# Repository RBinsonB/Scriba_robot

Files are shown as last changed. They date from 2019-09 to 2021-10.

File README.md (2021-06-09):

# Scriba robot
More information (such as components used, robot building and so on) can be found on the [Hackster page of the project.](https://www.hackster.io/robinb/scriba-robot-a-printing-robot-0048fa).

ROS code has been moved to dedicated repositories.
- [scriba_ros](https://github.com/RBinsonB/scriba_ros): robot base packages (for bringup, motor command, odometry)
- [scriba_localization](https://github.com/RBinsonB/scriba_localization): robot localization related packages (EKF, camera localization)

## Concept
Scriba is a printing robot. It prints on its wake, using the sheet edges and the printing in process as a reference for its navigation. It uses multiple cameras to correct its trajectory and printing alignment through a SLAM algorithm

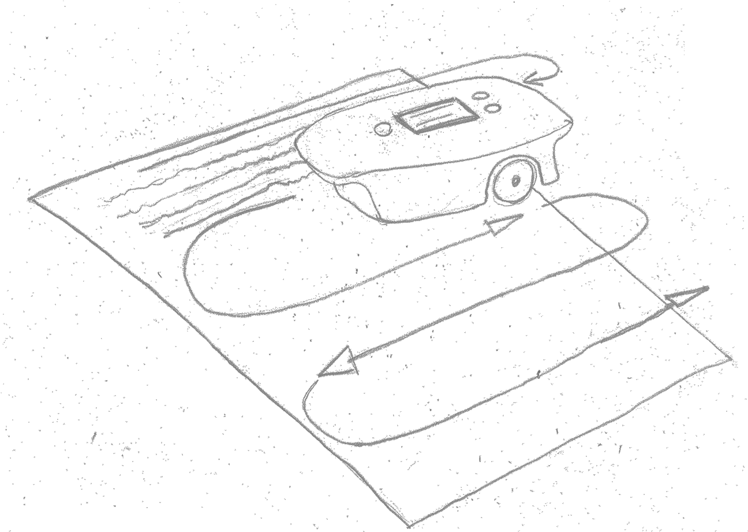
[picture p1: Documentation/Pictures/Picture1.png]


*Robot concept*

The robot was supposed to be light and portable but grew in sized as the project progressed. It is designed to print on medium and large surfaces.

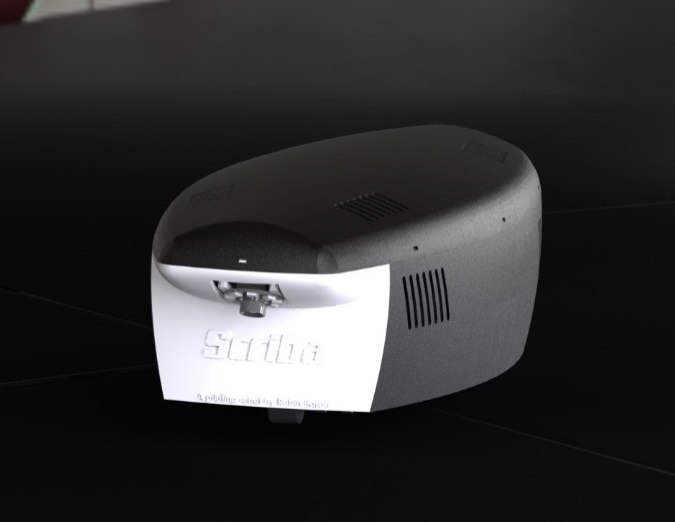
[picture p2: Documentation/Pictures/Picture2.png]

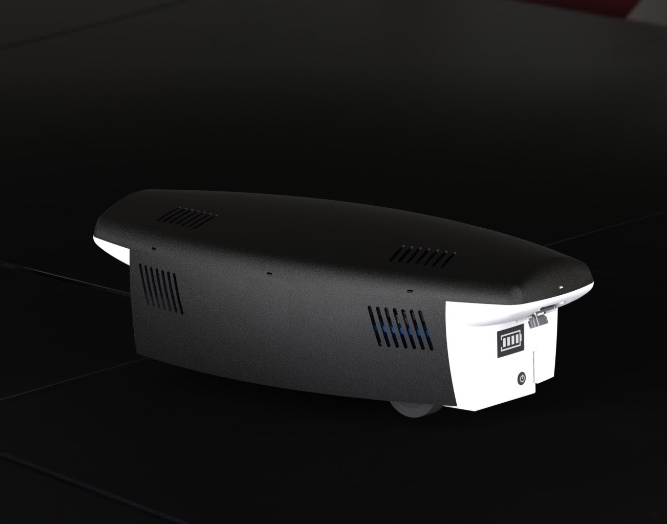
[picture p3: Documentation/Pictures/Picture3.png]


## Project advancement
WORK IN PROGRESS

Done:
```diff
+ Mechanical Design
+ Electrical Design
+ Components printing/machining
+ Robot assembly
+ PCB assembly
+ ROS serial communication with Arduinos
+ Standard motor command
+ Odometry
+ Odometry and motor command calibration
```
To do:
```diff
- Printhead test
- Low voltage disconnect board
- Step motor command
- Printing command
- Localization by camera
```
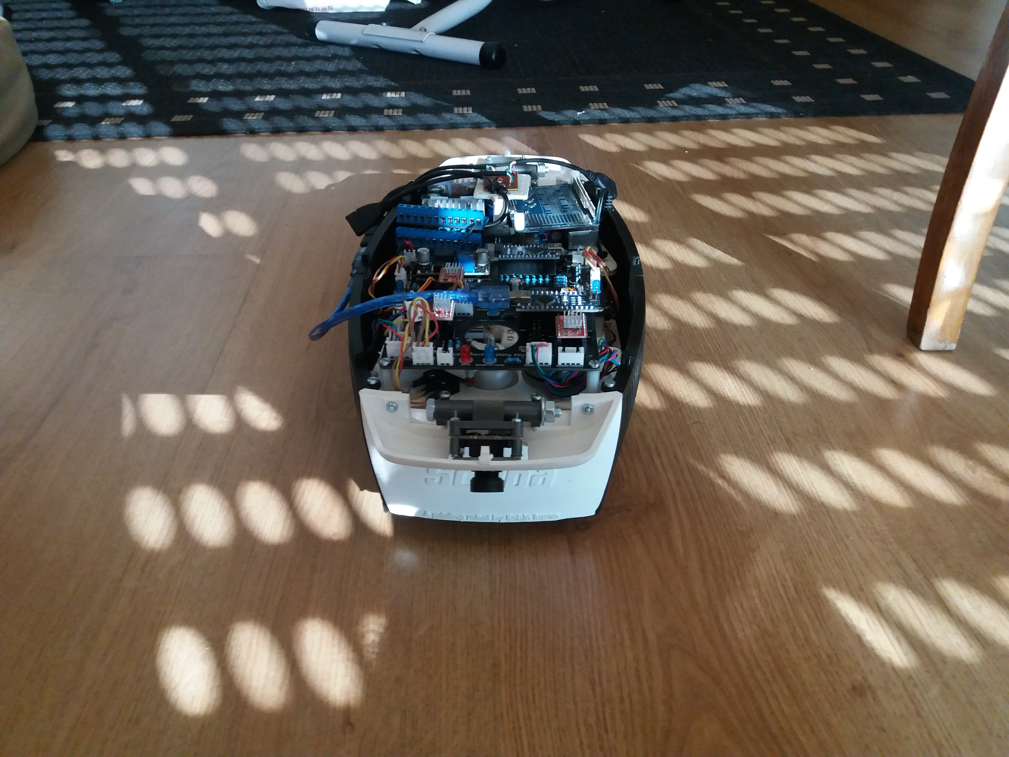
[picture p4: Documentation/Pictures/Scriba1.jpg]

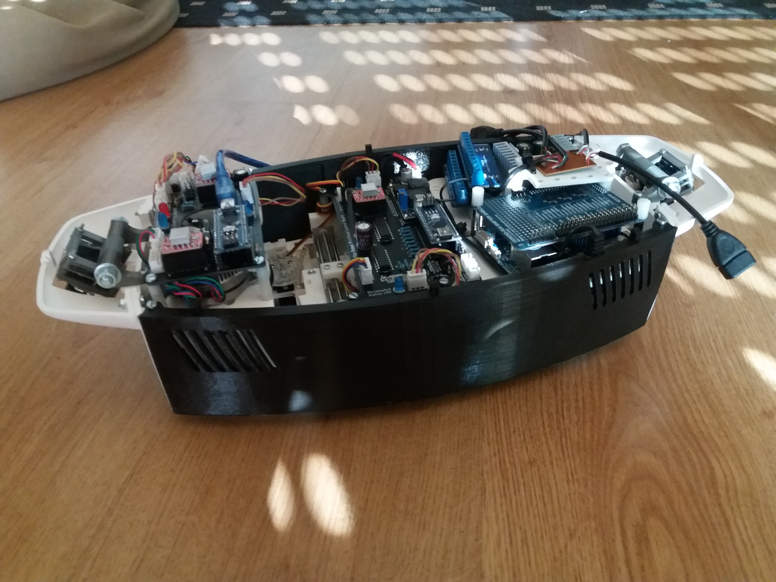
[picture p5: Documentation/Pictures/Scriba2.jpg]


### Video: Scriba drive & odometry test
Scriba odometry test (https://www.youtube.com/watch?v=UUCUU0tR3d4)
### Video: Scriba front wheel calibration 
Scriba front wheel angle calibration (https://www.youtube.com/watch?v=NhuQ65PKyDQ)

## System overview
The detailed [technical design description can be found here.](https://raw.githubusercontent.com/RBinsonB/Scriba_robot/master/Technical_Design_Scriba.pdf)

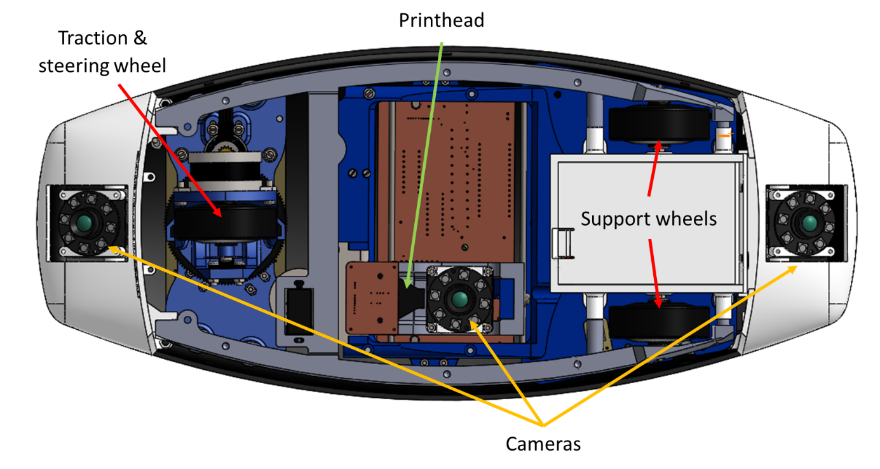
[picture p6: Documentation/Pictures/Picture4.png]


*Scriba robot bottom view*

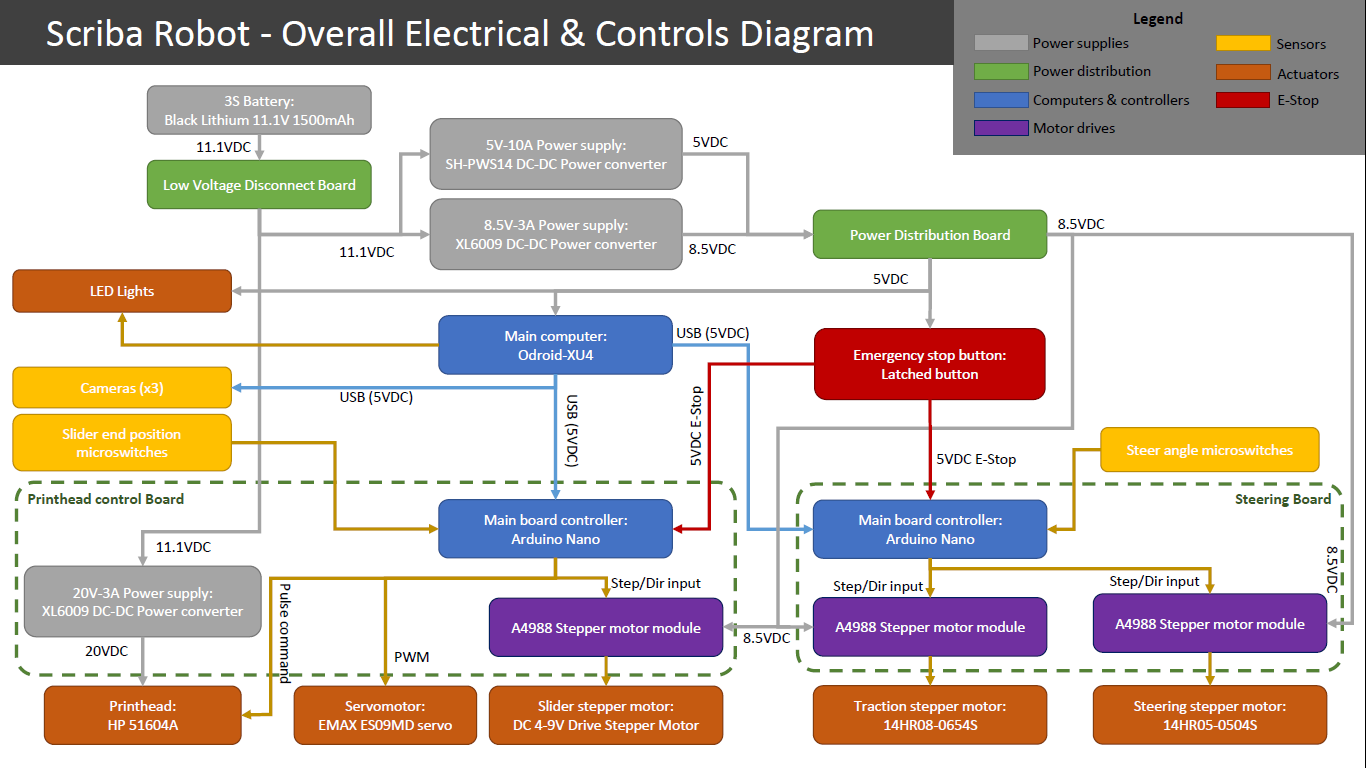
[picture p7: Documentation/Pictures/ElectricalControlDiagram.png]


*Overall electric & controls diagram*

[The diagram can be found here in higher resolution](https://raw.githubusercontent.com/RBinsonB/Scriba_robot/master/Overall_Electrical_&_Controls_Diagram_Scriba_Robot.pdf)

### Controls
The main computer of the robot is an Odroid-XU4 running Ubuntu 18.04 and mainly relying on a ROS (Robot Operating System) program to run the robot. Computer vision tasks are carried out by OpenCV programs interfaced with the ROS main program.

Actuator control is carried out by two Arduinos Nano, as they can handle real-time operation and GPIO control better than the main computer. They are connected to serial node on the ROS main program.
The robot can be controlled by WiFi from a remote computer by connecting to the Odroid-XU4 via SSH.

### Drive configuration
The robot has a steer drive configuration (also called steerable driving wheel configuration) with one powered and steering wheel at the front and 2 wheel for support at the rear (like a tricycle). This configuration was chosen because of the high driving accuracy it provides when following a navigation path.

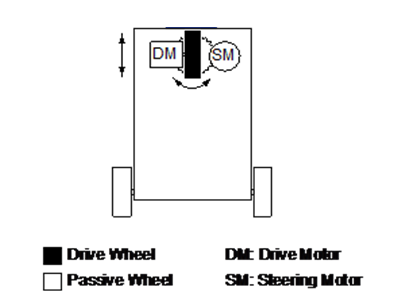
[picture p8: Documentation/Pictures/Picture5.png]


*Steer Drive configuration*

### Navigation & Localization system
The robot uses a SLAM algorithm (Simultaneous Localization And Mapping) to navigate. It localize itself by using the printing in process as a reference.

Cameras are located at the front and at the rear of the robot. Their location allows the robot to see the printing in process (with the rear camera) and the previous printing. Being able to see the previous printing after a turn is crucial to correct localization because turns generate a lot of imprecisions in the odometry.

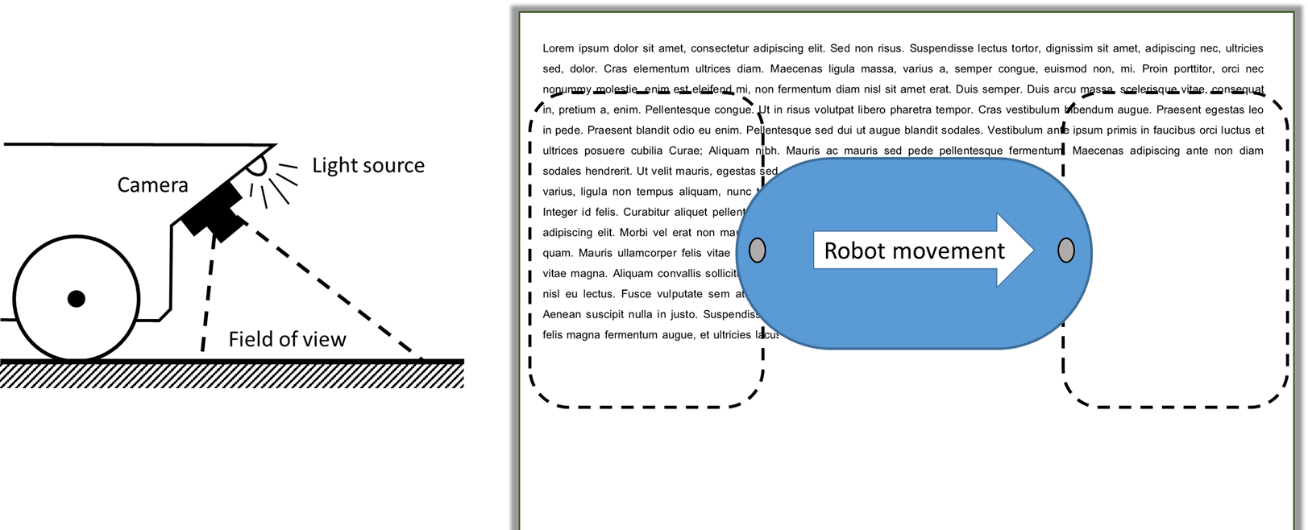
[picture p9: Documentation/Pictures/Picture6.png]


A light source near the camera ensures a correct and uniform lighting of the scanned surface. Inclination of the camera images is corrected by a homographic algorithm.

### Printing system
The printhead is placed on a sweeping system. Both have to stay perpendicular to the printing direction even when the robot is correcting its trajectory. The printing system is therefor able to rotate around the kinematic center of the robot.

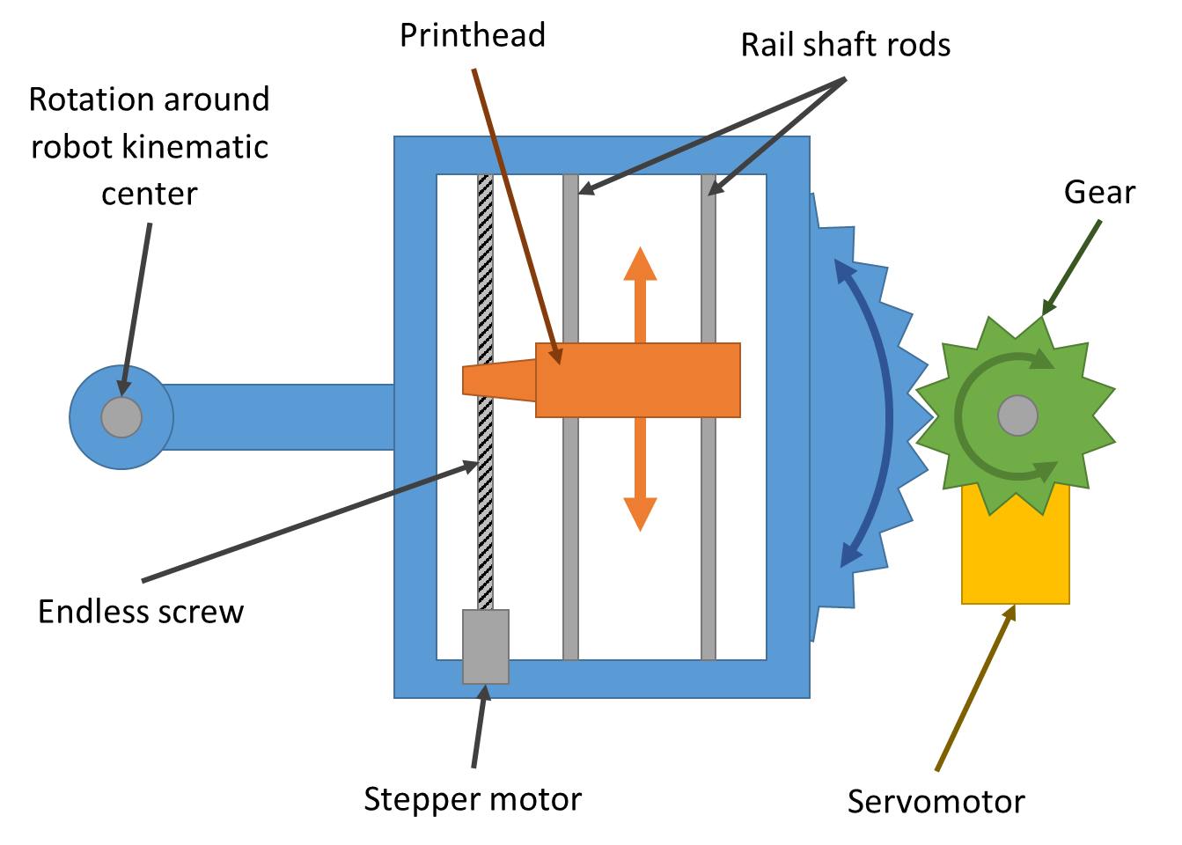
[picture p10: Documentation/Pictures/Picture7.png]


*Printing system schematics*

## Code description:
* Arduino: includes Arduino programs.
  * Programs:
    * *Scriba_steering_board_V1*: Program for the arduino of the drive unit. Uses custom message type to receive and execute motor commands, send odometry data and perform calibration operations.
    * *Scriba_steering_board_V2*: Updated version of the firmware to work with potentiometer on the front wheel steer angle.

## Authors

* **Robin Baran** - *Initial work*

## License

This project is licensed under the GNU General Public License version 3

## Acknowledgments

* [Inkjet Printer For the Reprap](https://reprap.org/mediawiki/images/1/1a/Inkjet.pdf) by Amberish Jaipuria
* [DIY Inkjet Printer](https://www.thingiverse.com/thing:8542/) by Patrick Hannan, Jared Knutzen, Nicholas C Lewis, Joy Markham

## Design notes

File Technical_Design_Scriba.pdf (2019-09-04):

Robin Baran | Scriba Robot - Technical Design | 1

## Scriba Robot – Technical Design

This document aims to describe the technical design of the Scriba robot. It includes mechanical design, electronics and code.

## Summary

## 1 Design Overview

### 1.1 Drive unit

1.1.1 Overall design
The traction and steering motor are assembled in a “drive unit” placed at the front of the robot.

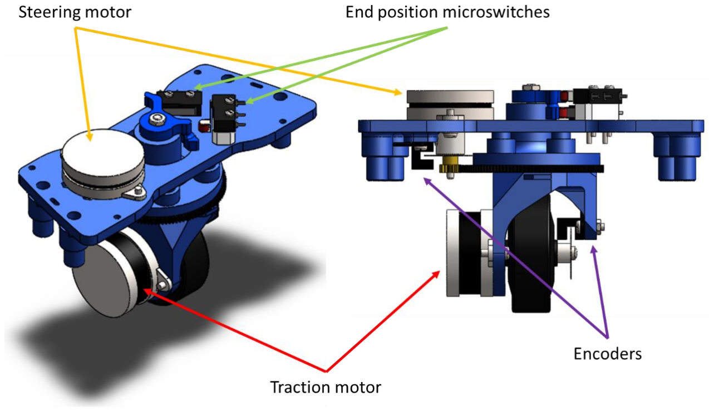
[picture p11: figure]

Figure 1: Drive unit

The driving wheel is powered by a stepper motor (14HR08-0654S) with a step angle resolution of 0.9 deg. In addition an encoder counts the rotation angle with a resolution of 1.8deg.

The driving wheel is steered by a stepper motor (14HR05-0504S) with a step angle resolution of 0.9 deg. In addition an encoder counts the rotation angle with a resolution of 1.8deg. The system is designed to rotate the driving wheel +/-90°.

Taking in account gears and microstepping configuration (rms), the relation between steering motor step and wheel angle (φ) is:

φ = steps ∗ angle by step ∗ rms ∗ (
zmot

zgear)

φ = steps ∗ rms ∗ 0.9 ∗ (

16
120) = steps ∗ rms ∗ 0.12

To recap the possible results:

Microstepping
configuration

Wheel angle (φ) for 1 step in degrees
Full step | 0.12°
1/2 step | 0.06°
1/4 step | 0.03°
1/8 step | 0.015°
1/16 step | 0.0075°

Two microswitches are used to detect the end position for calibration purposes: the starting angle of the wheel is unknown and a calibration is required before driving the robot. The microswitches are placed on slotted holes and can be adjusted.

1.1.2 Electronics
The stepper motors are controlled by an Arduino Nano and two A4988 modules. All those elements and connections for encoders, microswitches, and so on are integrated into a PCB (named “Steering Board”).

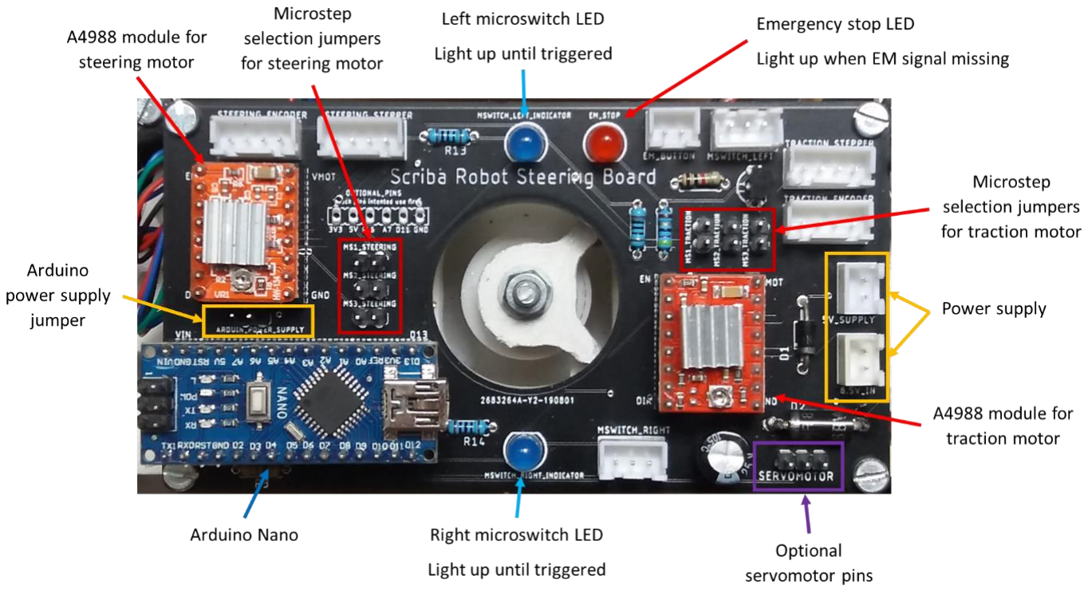
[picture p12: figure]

Figure 2: Steering Board

The board needs 5V and 8.5V power supplies. The 5V can be supplied by the Arduino if the Arduino power supply jumper is connected.

1.1.2.1 Microstepping selection
Stepper microstepping can be configured by the use of jumpers on the board. Connecting a jumper sets the microstep pin to high.

The truth table for the MS pins logic is the following:

MS1 MS2 MS3 | Microstep Resolution
Low | Low | Low | Full step
High | Low | Low | Half step
Low | High | Low | Quarter step
High | High | Low | Eighth step
High | High | High | Sixteenth step

1.1.2.2 Emergency stop
An emergency stop feature prevents the motors from running without a 5V input on the emergency stop connector. The emergency stop red LED lights when the signal is absent.

1.1.3 Program & Control
The unit is driven by an Arduino Nano. The Arduino is connected to the main computer of the robot, the Odroid-XU4 by USB.

The program on the Arduino connects to a serial node of the ROS main program.

### 1.2 Printing system

1.2.1 Overall design
The printing system is assembled on a rotating support (rotating around the robot kinematic center) to correct the alignment if needed.

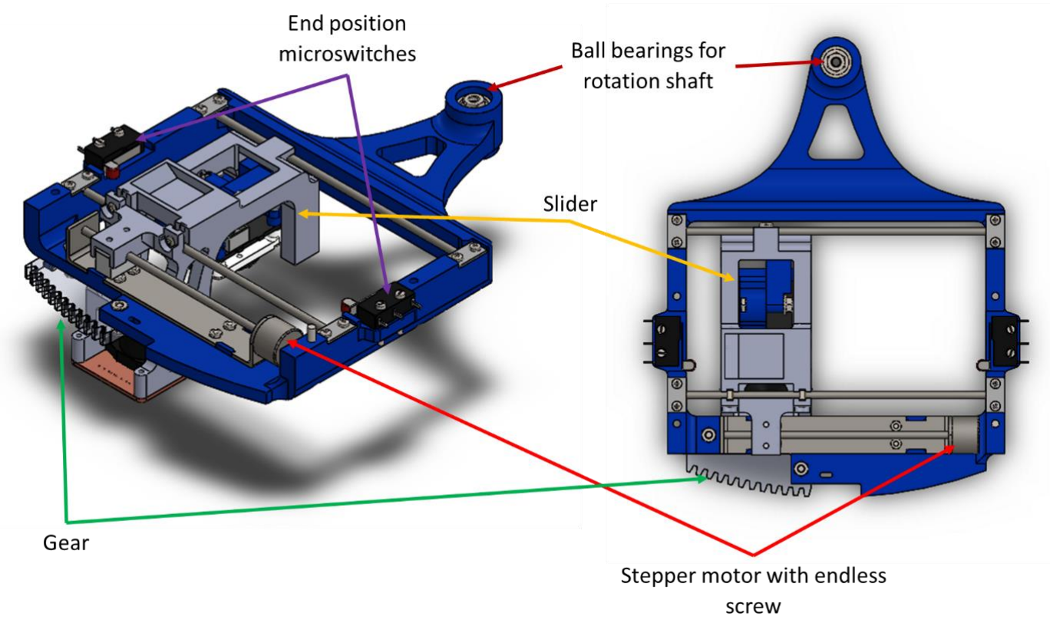
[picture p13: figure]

Figure 3: Printing system

The printhead is placed on a “slider”, giving the system an 83mm sweeping length. The slider is powered by a stepper motor (DC 4-9V Drive Stepper Motor Screw With Nut Slider 2 Phases 4 Wires) with a resolution of 0.18°/step. The endless screw has a resolution of 0.5mm/turn making the overall system to have a resolution of 0.025mm/step.

Taking in account the microstepping configuration:

Microstepping
configuration

Slider displacement for 1 step

Full step | 0.025mm
1/2 step | 0,0125mm
1/4 step | 0,00625mm
1/8 step | 0,003125mm
1/16 step | 0,0015625mm

Two microswitches are used to detect the end position for calibration purposes. The starting position of the stepper motor is indeed unknown and needs to be calibrated.

1.2.2 Printhead
The printhead used by the robot is an inkjet printhead HP 51604A. It has been chosen for its ease of use and low price. Hacked inkjet printhead with easy controls are difficult to find. The HP 51604A (and the HP C6602) have a good documentation available online.

Most information on how to control the printhead came from Inkjet Printer For the RepRap by Amberish Jaipuria (https://reprap.org/mediawiki/images/1/1a/Inkjet.pdf), itself using as a primary source Inkjet Applications by Gilliland, M.

The printhead can only print in one color (black) with no possibility of half-toning. The printhead features 12 nozzles spanning over 3.2mm.

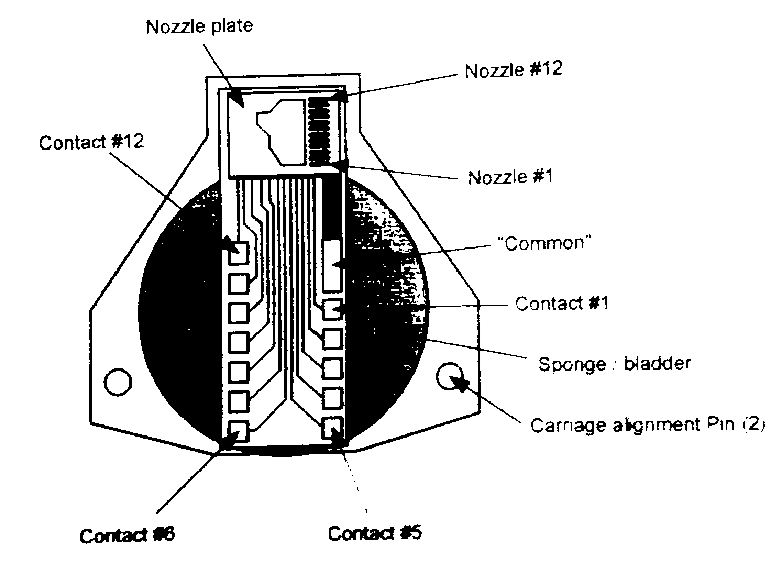
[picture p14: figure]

Figure 4: HP 51604A Printhead contacts & nozzles

Each nozzle has a 65Ω resistor and fires when a pulse is put across the resistor. The total energy released during the pulse has to be around 40µ Joules.

Taking in account the following equation:

Pulse widtℎ =

resistance ∗ energy
voltage² =

0.65 ∗ 0.00004
voltage

2

Gilliand M. calculated the optimal pulse widths and voltages and provides the following table:

Voltage (VDC) Pulse width (µs) 20 6.5
21 6
22 5.5
23 5
24 4.5

Those pulse width are optimal. A too short pulse time can result in low droplet quality or clogged nozzles. A too long pulse time can burn the nozzle resistor.

It’s also recommended to wait at least 800µs before firing again the same nozzle. Two adjacent nozzles cannot be fired simultaneously and only two nozzles on the whole printhead can be fired simultaneously. Moreover it is recommended to wait 0.5µs between each nozzle pair being fired.

A PCB (“Printhead Contact Board”) allows for a stable and easy connection between the nozzle contacts and the wires from the controller.

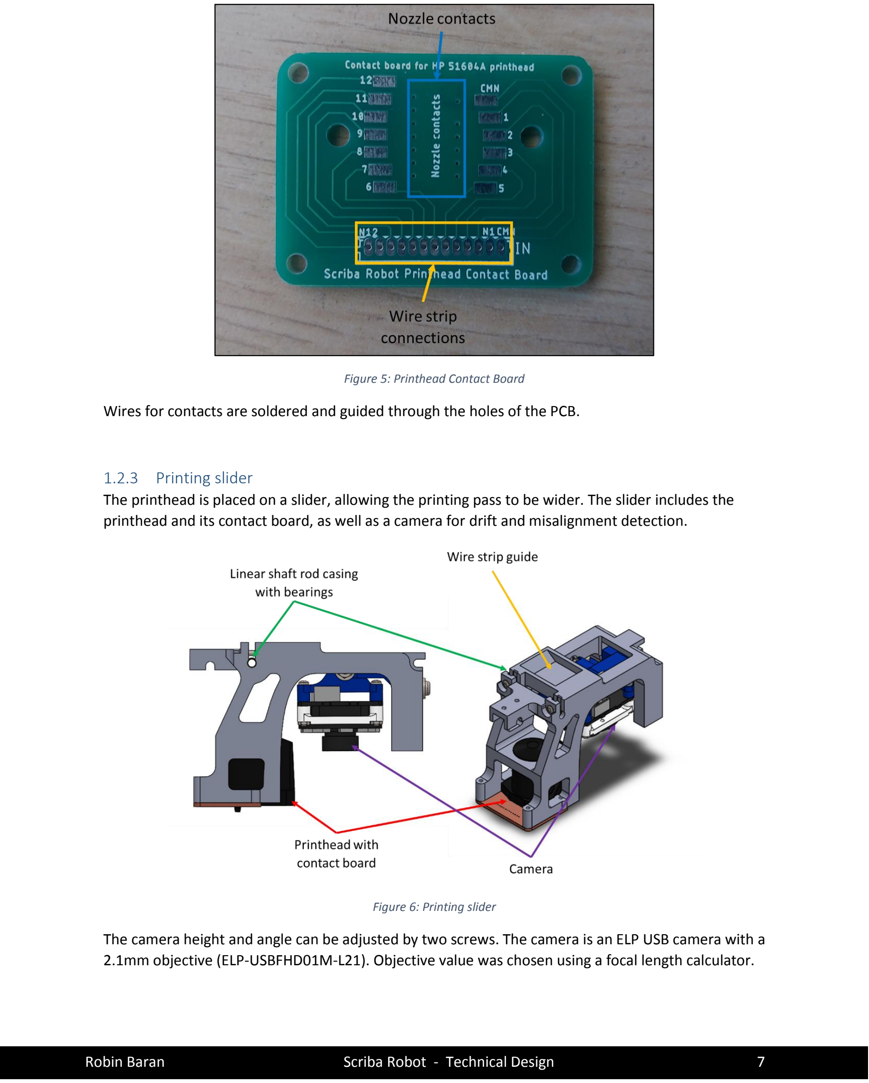
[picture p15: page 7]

Figure 5: Printhead Contact Board

Wires for contacts are soldered and guided through the holes of the PCB.

1.2.3 Printing slider
The printhead is placed on a slider, allowing the printing pass to be wider. The slider includes the printhead and its contact board, as well as a camera for drift and misalignment detection.

Figure 6: Printing slider

The camera height and angle can be adjusted by two screws. The camera is an ELP USB camera with a 2.1mm objective (ELP-USBFHD01M-L21). Objective value was chosen using a focal length calculator.

1.2.4 Alignment & Correction
The printing system needs to correct the eventual robot misalignment and drift from the intended position to ensure a good print quality. This error correction can be split in three items
- Forward/backward drift (ex⃗
)
- Lateral drift (ey⃗⃗
)
- Alignment (λ)

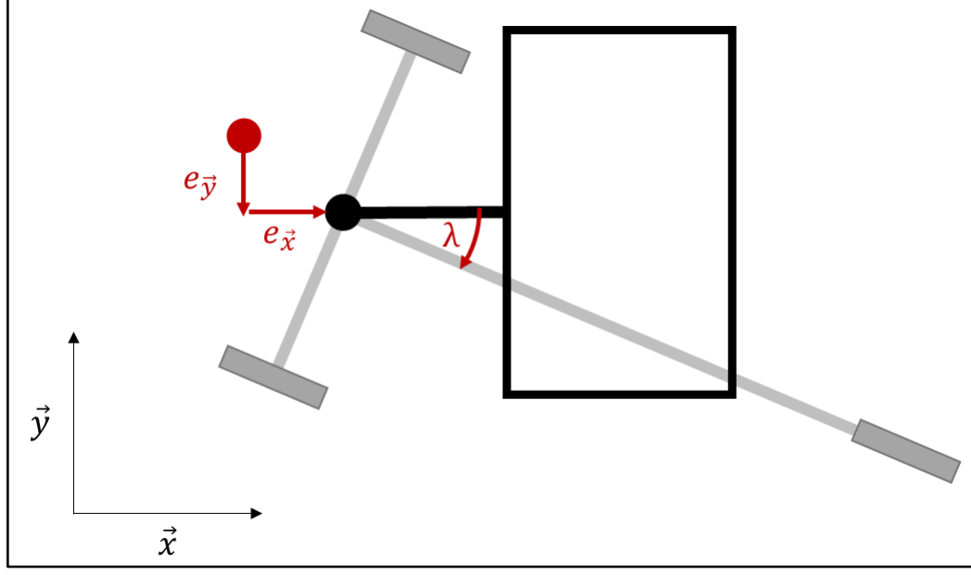
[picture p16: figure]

Figure 7: Printing system pose error

1.2.4.1 Forward/backward drift
There is no actuator for correcting an error in the printing direction (robot driving direction). The system relies instead on “shiftting” the nozzles used. A least 1 nozzle on each end of the printhead needs to be reserved for this operation and therefore reduces the overall nozzle span.

1.2.4.2 Lateral drift
Lateral drift is simply corrected by adding an offset on the slider starting position. A specific length on both sides has to be reserved for this operation and therefore reduces the slider course.

1.2.4.3 Alignment
The printing system can rotate slightly around the robot kinematic center to correct its alignment. A servomotor is used to control the rotation. The gear ratio between the servomotor and the printing system is 18/244.

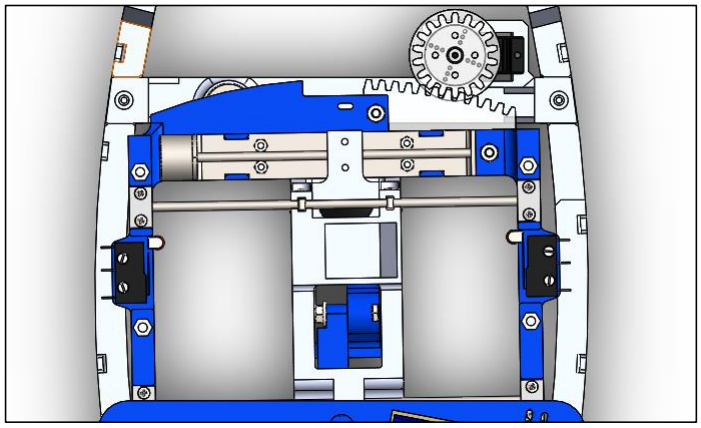
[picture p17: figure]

Figure 8: Printing system gears & servomotor, top view

1.2.5 Electronics
The printhead nozzles are controlled by two ULN2803 Darlington arrays to interface the Arduino outputs with the 20V power supply. For each nozzle a pull-down 1kΩ resistor is added to ensure a good control of the firing pulse time.

The stepper motor for the slider is controlled by an Arduino Nano and an A4988 module.

All those elements, as well as the 20V power converter and the connections for the end position microswitches are integrated into a PCB (named “Printhead Control Board”).

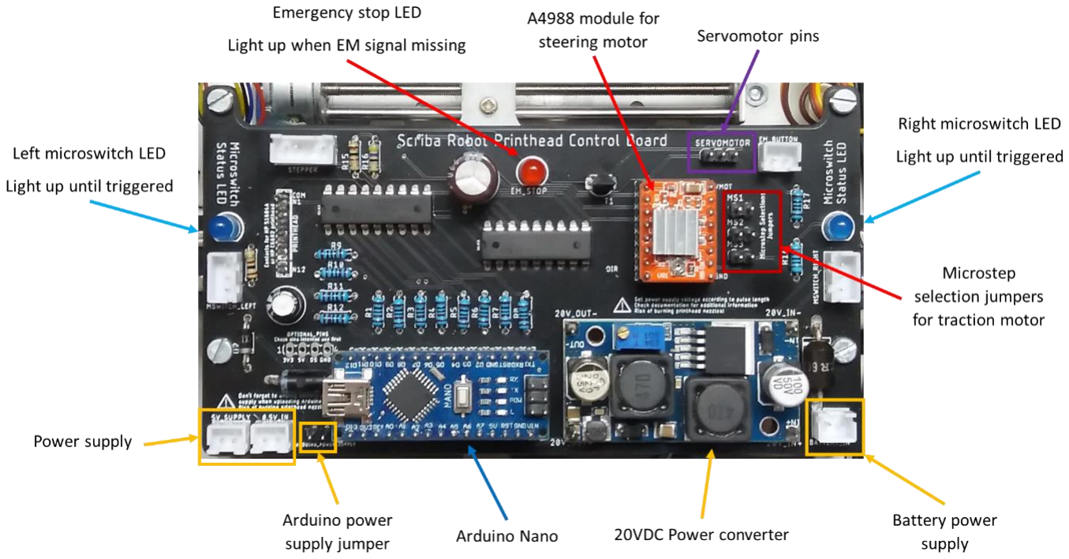
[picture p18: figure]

Figure 9: Printhead Control Board

The board needs 5V and 8.5V power supplies as well as a connection to the battery. The 5V can be supplied by the Arduino if the Arduino power supply jumper is connected.

1.2.5.1 Microstepping selection
Stepper microstepping can be configured by the use of jumpers on the board. Connecting a jumper sets the microstep pin to high.

The truth table for the MS pins logic is the following:

MS1 MS2 MS3 | Microstep Resolution
Low | Low | Low | Full step
High | Low | Low | Half step
Low | High | Low | Quarter step
High | High | Low | Eighth step
High | High | High | Sixteenth step

1.2.5.2 Emergency stop
An emergency stop feature prevents the motors from running without a 5V input on the emergency stop connector. The emergency stop red LED lights when the signal is absent.

1.2.6 Program & Control
The unit is driven by an Arduino Nano. The Arduino is connected to the main computer of the robot, the Odroid-XU4 by USB.

The program on the Arduino connects to a serial node of the ROS main program.

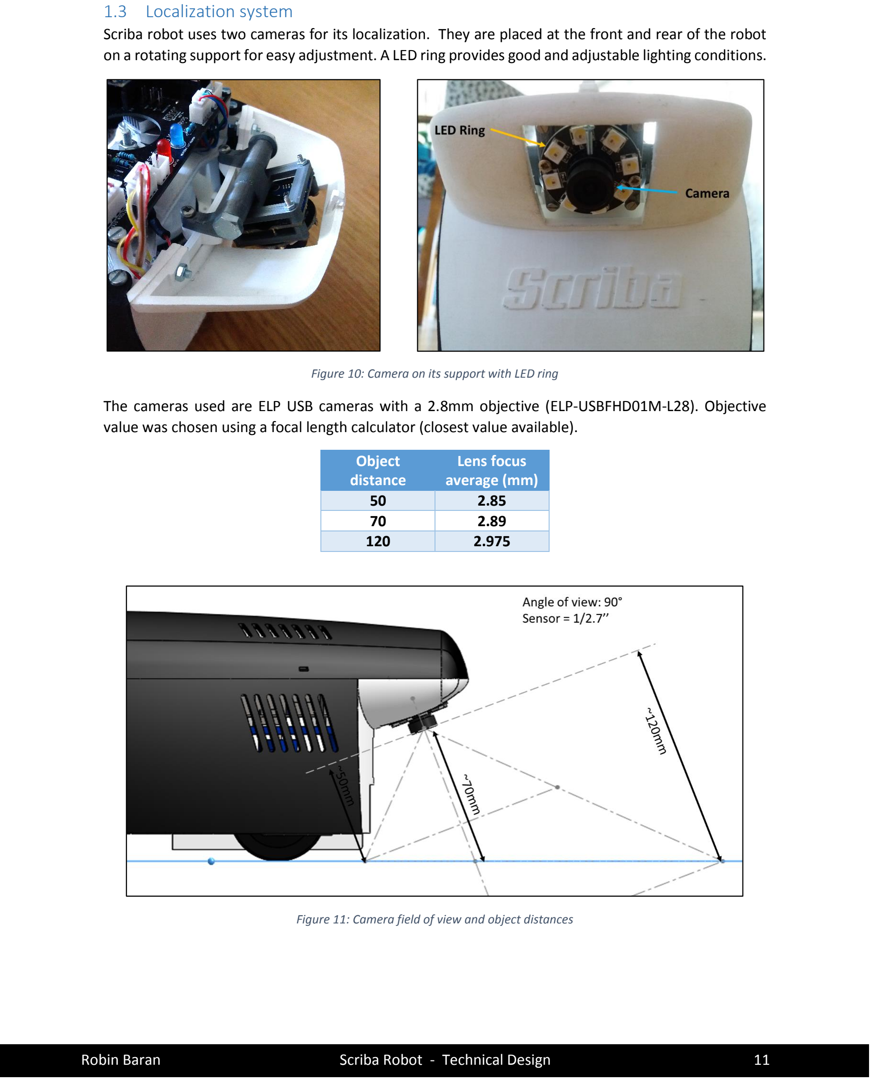
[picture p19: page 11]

### 1.3 Localization system

Scriba robot uses two cameras for its localization. They are placed at the front and rear of the robot on a rotating support for easy adjustment. A LED ring provides good and adjustable lighting conditions.

Figure 10: Camera on its support with LED ring

The cameras used are ELP USB cameras with a 2.8mm objective (ELP-USBFHD01M-L28). Objective value was chosen using a focal length calculator (closest value available).

Object
distance

Lens focus
average (mm)
50 2.85
70 2.89
120 2.975

Figure 11: Camera field of view and object distances

### 1.4 Power distribution

Three different voltages are used by the robot components: 5V, 8.5V and ~20V. Power is provided by a 3S battery (Black Lithium 11.1V 1500mAh) and then converted and distributed to the different elements.

The battery and converters are placed at the rear of the robot to keep the majority of the weight as close as possible to the kinematic center to minimize drift.

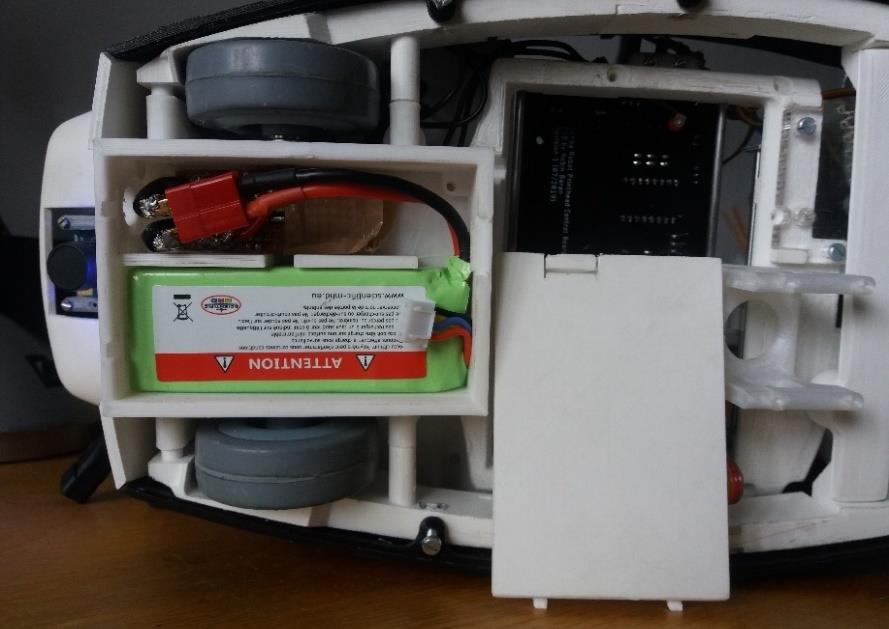
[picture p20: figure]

Figure 12: Battery case and connection

A first board connects to the battery and distributes the power to the power converters and battery level display. The output power from the power converters (5V and 8.5V) is then supplied to another PCB (“named PowerOut” or “Power Distribution Board”) with screw terminals for easy distribution to other elements. This board also includes a 1000µF capacitor on each voltage to smooth current spikes.

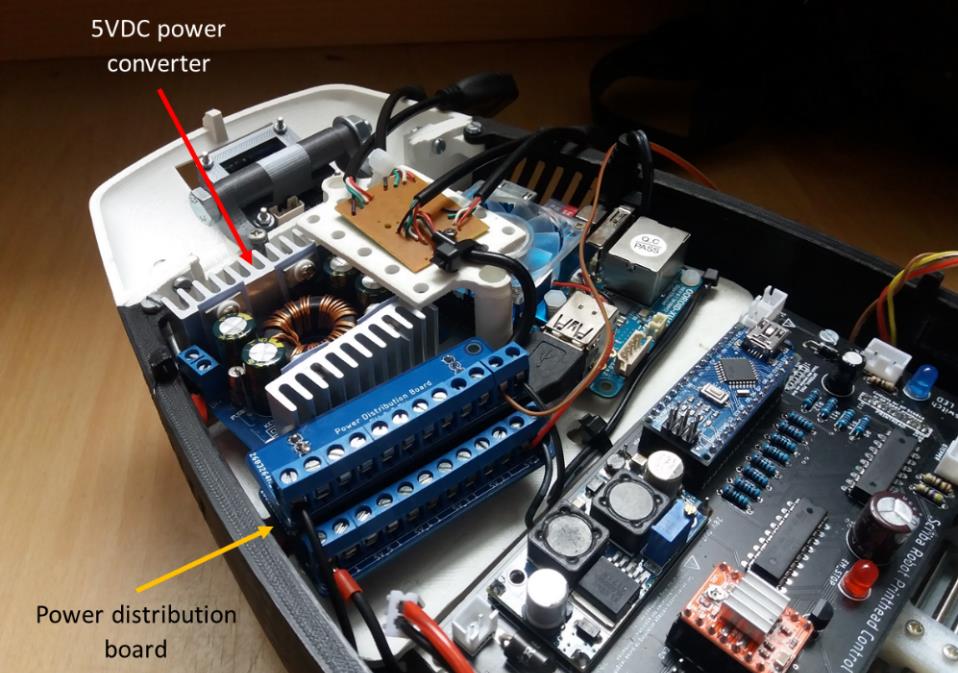
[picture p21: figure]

Figure 13: Power distribution board on the robot

The battery board will be replaced by a LVD (Low Voltage Disconnect) board with a relay/transistor in the future.

## 2 Robot Model

Before implementing any navigation feature, the robot needs to be modeled. The model is not only useful for visualization purposes but also essential for frame transforms and other calculations.

For a ROS implementation two models are needed:

- Kinematic model: needed for odometry and move command.
- CAD model (URDF): base on the kinematic model, needed for visualization and frame transforms.

### 2.1 Kinematics

The kinematics equations of the robot are needed to implement move command and odometry.

All kinematic equations are described in the document “Kinematics_Scriba”.

### 2.2 URDF

ROS uses URDF (Unified Robot Description Format) files to describe robot models. Those models are described using a kinematic logic, with “links” (parts) connected through “joints” of different types (rotation, translation …).

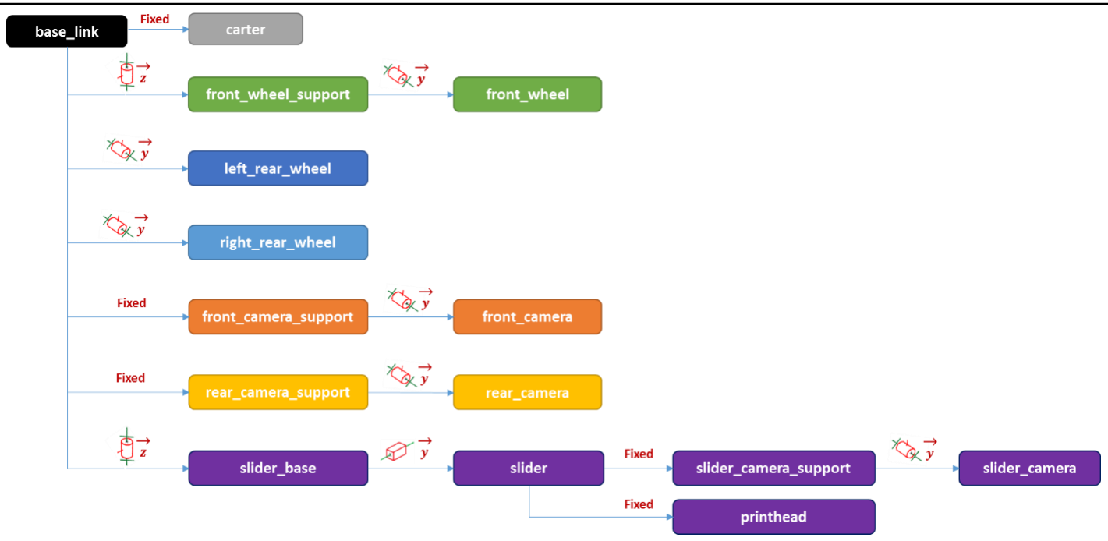
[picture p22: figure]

Figure 14: Scriba robot simplified kinematic diagram

The URDF file and other files needed for visualization are included in the ROS package “scriba_description”.

## 3 Navigation

### 3.1 Calibration

An accurate model is essential for odometry and navigation commands. The model therefore needs to be calibrated to ensure an optimal navigation.

The three variables to calibrate are:

- Front wheel angle offset
- Front wheel radius
- Robot’s length (distance between the kinematic center and the front wheel)

All values are dependent on each other and as such it is possible to get a better calibration by repeating the operations a second time.

3.1.1 Front wheel angle offset
Before calibrating the front wheel angle offset it’s necessary to run a script to put the wheel at position zero.

The robot main program is launched first using the bringup launch file:

And the following script is run on another terminal (0 as wheel offset):

rosrun scriba scriba_front_wheel_calibration.py

The robot can then be placed on a straight and visible line (on a floor pattern for example) and driven in a straight line using the teleop keyboard.

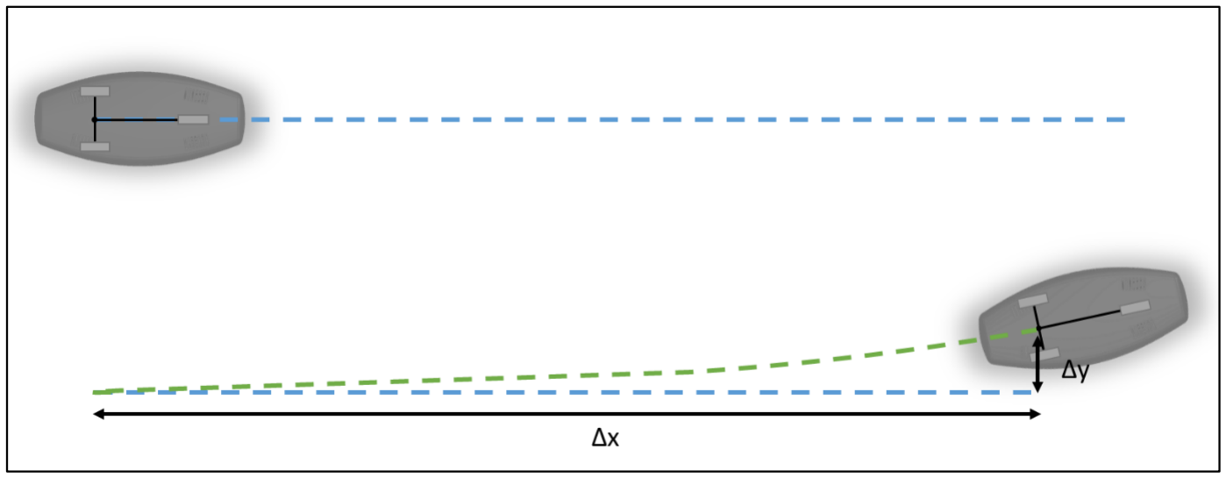
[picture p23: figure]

Figure 15: Difference between odometry and real value due to front wheel angle offset

By using the following equation (from the document “Kinematic_Scriba”) the front wheel angle can be calculated and corrected by an offset:

φ = arctan(L ∗
2 ∗ arctan (

Δy
Δx

)

d⏜wr | )

d⏜wr being the reported x-displacement in the odometry in this situation.

roslaunch scriba scriba_bringup.launch

3.1.2 Front wheel radius
Once the front wheel angle calibrated the wheel radius can be calibrated as well.

The robot main program is relaunched first using the bringup launch file:

And the following script is run on another terminal (with the previous calculated offset as wheel angle offset):

rosrun scriba scriba_front_wheel_calibration.py

The robot can then be placed on a straight and visible line (on a floor pattern for example) and driven in a straight line using the teleop keyboard.

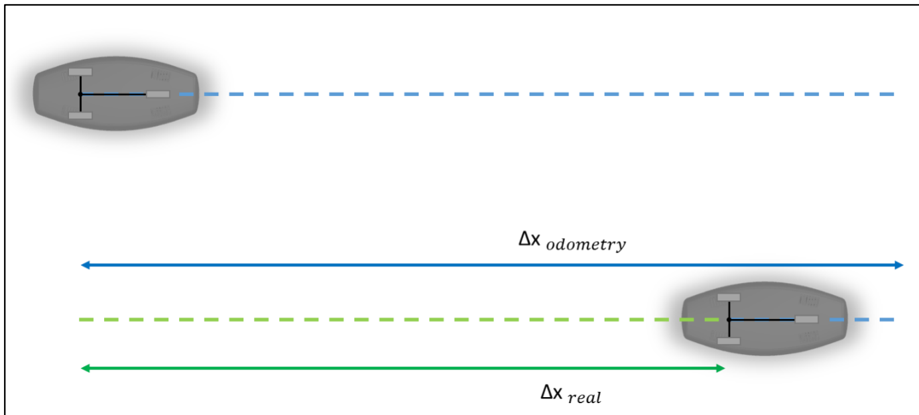
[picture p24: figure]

Figure 16: Difference between odometry and real displacement due to front wheel radius inaccuracy

The calibrated wheel radius is given by the following formula:

radiuswℎeel = radiuswℎeel ∗

Δx
odometry
Δx
real
Δx

odometry being the reported x-displacement in the odometry.

Δx

real being the measured x-displacement

3.1.3 Robot’s length
At last the robot’s length value needs to be calibrated. Length refers here to the distance between the front wheel and the robot’s kinematic center.

The robot main program is relaunched first using the bringup launch file:

roslaunch scriba scriba_bringup.launch

roslaunch scriba scriba_bringup.launch

And the following script is run on another terminal (with the previous calculated offset as wheel angle offset):

rosrun scriba scriba_front_wheel_calibration.py

The robot can then be placed on a straight and visible line (on a floor pattern for example) and driven in circle using the teleop keyboard (maximum rotation: front wheel angle of π
2

⁄ to rotate around the
kinematic center).

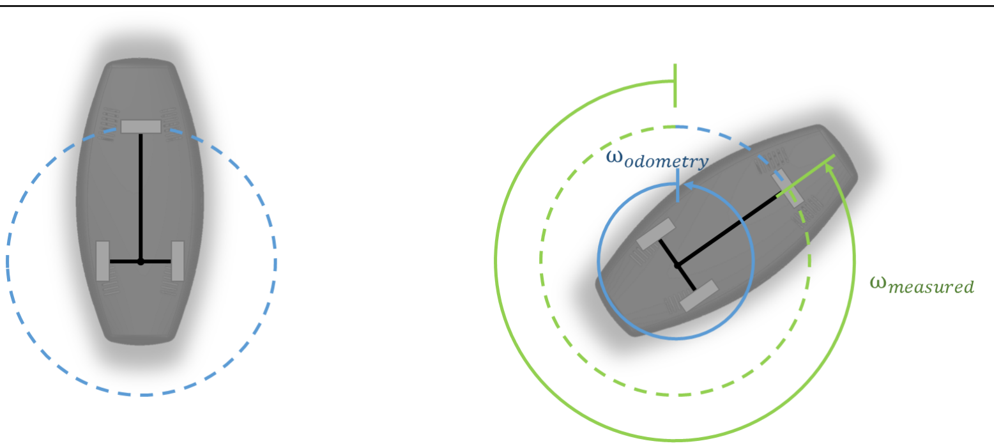
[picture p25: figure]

Figure 17: Difference between odometry and real angle due to robot length inaccuracy

The calibrated length is given by the following formula:

L = L ∗

ωodometry

ωreal

ωodometry being the reported z-angle in the odometry (be careful, angles are reported as quaternion in ROS).

ωreal being the measured angle.

### 3.2 Odometry

The odometry (or “dead reckoning”) refers to the estimation of a robot position through its motion sensors data. The odometry is a relative position estimation (relative to the starting position) and suffers from the accumulation of sensor uncertainties, preventing it from being efficient over a long time period. Odometry is often use in combination with an absolute position estimation (such as a camera using external element as reference points).

In Scriba, the odometry is computed by the main computer with data from the Arduino of the drive unit. The node “scriba_odometry_broadcaster” in the “scriba” package subscribes to the topic /data_odom to receive the odometry data.

The odometry data is transmitted on the topic in a custom message type “odom_data” (from the “scriba_msgs” package) including:

- Time stamp
- Front wheel angle (at the beginning of the sample)

- Front wheel angle (at the end of the sample)
- Front wheel traveled steps
- Sample duration

The position is estimated using this data and the previous position.

The odometry data currently uses only stepper motor commands. Encoders are wired but not yet used due to the limited memory available in the Arduino Nano of the drive unit. They will be added if the odometry quality needs to be improved.

### 3.3 Localization

The localization refers to the absolute position estimation (using external references) used to correct the odometry position estimation.

WIP – Algorithm is not finished yet.

### 3.4 Move commands

Two drive modes are used by the robot:

- Standard mode, used when turning and moving to the next printing position.
- Printing mode, used when printing: low speed and steps command.

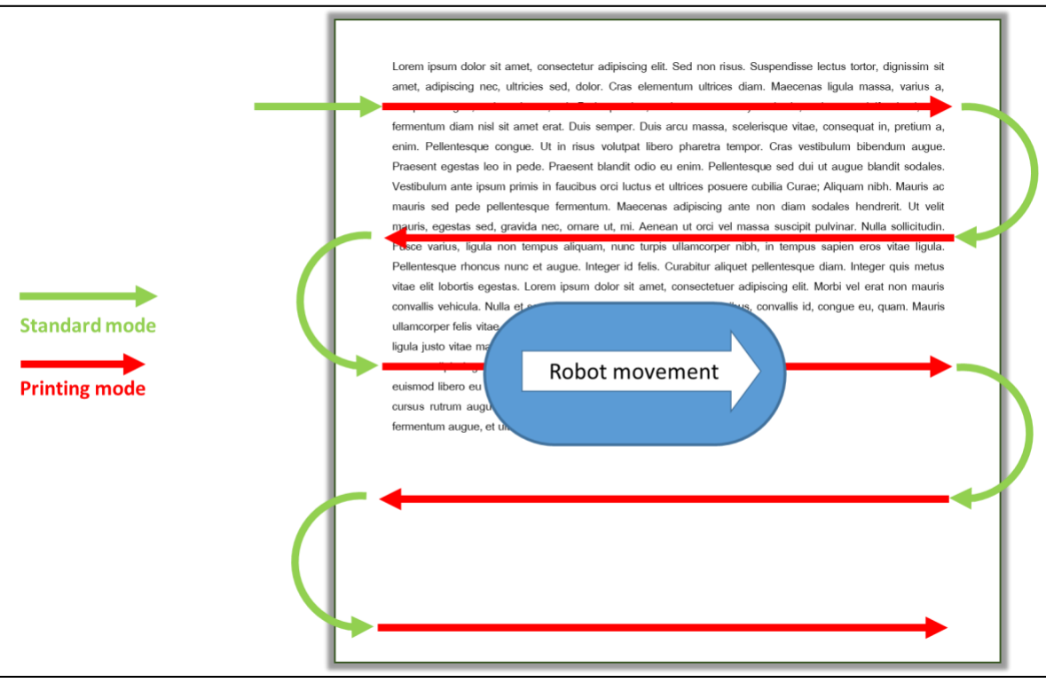
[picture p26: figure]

Figure 18: Robot driving modes

WIP – Printing mode not implemented yet.

## Table of figures

Figure 16: Difference between odometry and real displacement due to front wheel radius inaccuracy

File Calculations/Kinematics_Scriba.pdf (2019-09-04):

Robin Baran | Scriba Robot - Kinematics | 1

## Scriba Robot – Kinematics

This document describes the kinematic model & equations needed for the Scriba robot.

## Summary

## 1 General equations

The kinematics equations of the robot are needed to implement move command and odometry.

ROS move command is sent as a velocity (kinematic center speed) and twist (angular speed) command.

There are two main configurations to consider:

- Steering wheel with no angle
- Steering wheel with angle

In both cases we want to express the angle of rotation and the kinematic center displacement relative to the front wheel angle and front wheel displacement.

### 1.1 Steering wheel with no angle

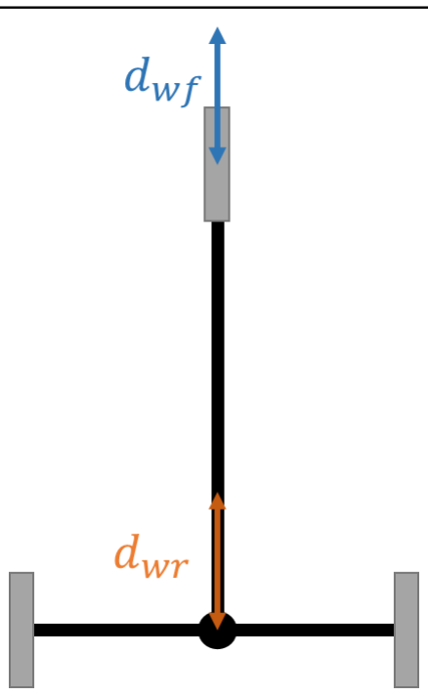
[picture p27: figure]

Figure 1: Kinematics with straight front wheel

It’s easy to get the angle of rotation and the kinematic center displacement relative to the front wheel angle and front wheel displacement:

- | Angle of rotation: | ω = 0
- | Kinematic center displacement: | dwr = dwf

### 1.2 Steering wheel with angle

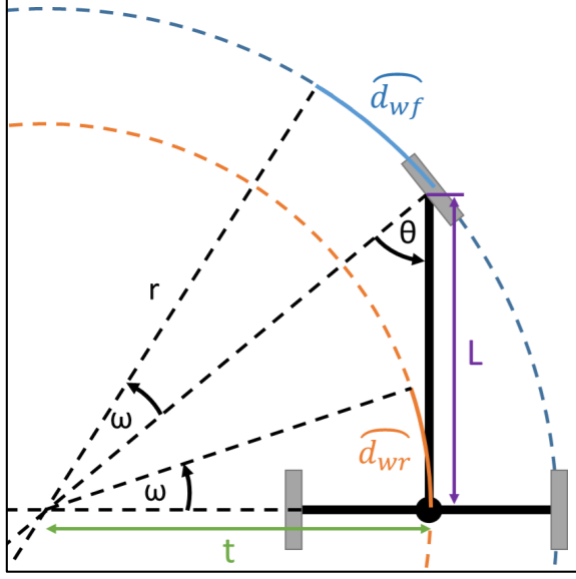
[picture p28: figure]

Figure 2: Kinematics with steered front wheel

tan(θ) =

t
L

⇔ t = L ∗ tan(θ)

cos(θ) =

L
r

⇔ r =

L
cos(θ)

d⏜wf = ω ∗ r =

ω ∗ L
cos(θ)

⇔ ω = d⏜wf ∗

cos(θ)
L

d⏜wr = ω ∗ t = ω ∗ L ∗ tan(θ) = d⏜wf ∗

cos(θ)
L

∗ L ∗ tan(θ) = d⏜wf ∗ cos(θ) ∗ tan(θ)

From those equations we obtain the angle of rotation and the kinematic center displacement relative to the front wheel angle and front wheel displacement:

- | Angle of rotation: | ω = d⏜wf ∗ cos(θ)
| | L
- | Kinematic center displacement: | d⏜wr = d⏜wf ∗ cos(θ) ∗ tan(θ)

## 2 Velocity command

ROS command outputs a kinematic center speed and an angular speed. On the other end the motor controls need a front wheel angle and a front wheel speed.

Therefore, command for the robot has to be expressed as a front wheel angle and front wheel speed relative to the angular speed and the kinematic center speed.

The front wheel angle sent as a motor command is φ and is expressed as:

φ =

π
2

− θ ⇔ θ =

π
2

− φ

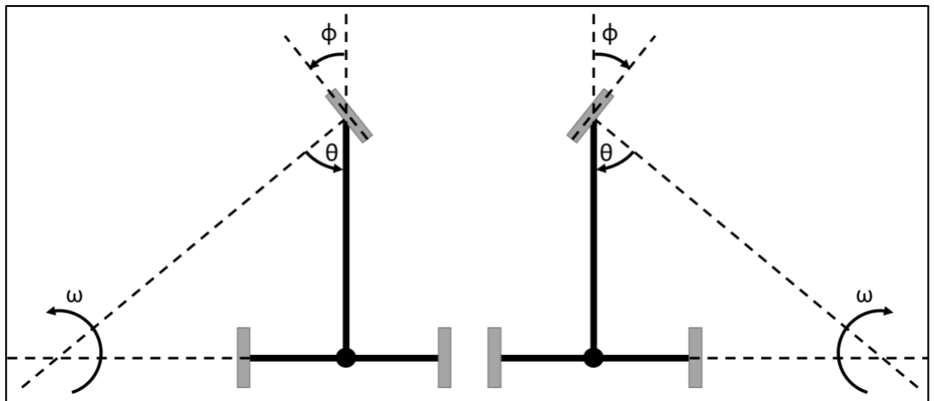
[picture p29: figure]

### 2.1 No angular speed command

In the special case of a command with no angular speed.

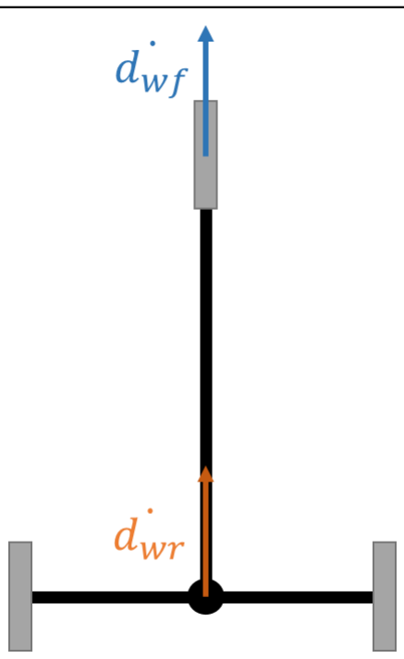
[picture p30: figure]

Figure 3: Velocities with straight front wheel

- | Front wheel rotation: | φ = 0
- | Front wheel speed: | dwḟ = dwr ̇

### 2.2 With angular speed command

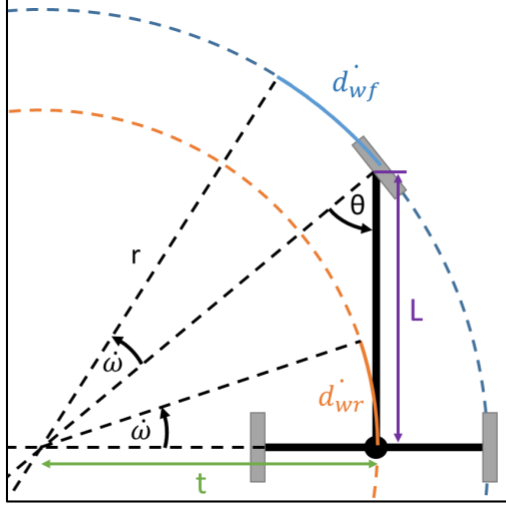
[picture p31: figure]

Figure 4: Velocities with steered front wheel

Using the previous equations (1.2 Steering wheel with angle - page 3) the following equations are derived:

d⏜wr = ωL tan(θ)

⟺ dwr

̇ = ω̇L tan(θ) + ω̇L θ̇(1 + tan
2
(θ))

And

d⏜wr = d⏜wf cos(θ) tan(θ)

dwr

̇ = dwḟ cos(θ) tan(θ) + d⏜wf θ̇(cos(θ)(1 + tan
2
(θ)) − sin(θ) tan(θ))

dwr

̇ = dwḟ sin(θ) + d⏜wf θ̇(cos(θ) + sin(θ) tan(θ) − sin(θ) tan(θ))

dwr

̇ = dwḟ sin(θ) + d⏜wf θ̇cos(θ)

Θ is considered constant for several reasons. Controlling both the front wheel angle and the front wheel angular speed is unpractical. Indeed the base controller would need the exact front wheel angle and the communication time with the Arduino sending that data is too long. Moreover, the front wheel angular speed will be very small in practice.

If θ constant then θ̇ = 0, the previous equations can be rewritten:

dwr

̇ = ω̇L tan(θ) = ω̇Ltan (

π
2

− φ) =

ω̇L
tan(φ)

⇔ tan(φ) =

ω̇L

dwr

̇

⇔ φ = atan (
ω̇L

dwr

̇

)

dwr

̇ = dwḟ cos(θ) tan(θ) = dwḟ cos (

π
2

− φ) tan (

π
2

− φ) = dwḟ sin(φ)

cos(φ)
sin(φ)

= dwḟ cos(φ) ⇔ dwḟ =

dwr

̇
cos(φ)

- | Front wheel rotation: | φ = atan (

ω̇ L
| | dwṙ

)

- | Front wheel speed: | dwḟ = dwṙ cos(φ)

### 2.3 Only angular speed command

Another special case is needed if only angular speed is required. Indeed, for an angle of φ =

π
2

⟶
cos(φ) = 0 and dwḟ =
| dwṙ cos(φ) | would go to infinite.

Using the previous equations (1.2 Steering wheel with angle - page 3) the following equations are derived:

| | ω = d⏜wf ∗

cos(θ)
L
| | ω̇ = dwḟ ∗ cos(θ) L
+

d⏜wf

L

∗ (−θ̇ sin(θ))

If θ constant then θ̇ = 0, the previous equations can be rewritten:

| ω̇ = dwḟ ∗ | cos(θ) L = dwḟ ∗

sin (

π
2

− φ)

L

= dwḟ ∗

sin(φ)
L
| | ⇔ dwḟ =

ω̇L
sin(φ)
- | Front wheel rotation: | φ = π
| | 2

or −

π
2
- | Front wheel speed: | dwḟ =

ω̇ L
sin(φ)

## 3 Odometry

In ROS, a 2D odometry is expressed as a displacement on the x-axis, a displacement on the y-axis and a rotation around the z-axis, all expressed in a global odometry frame.

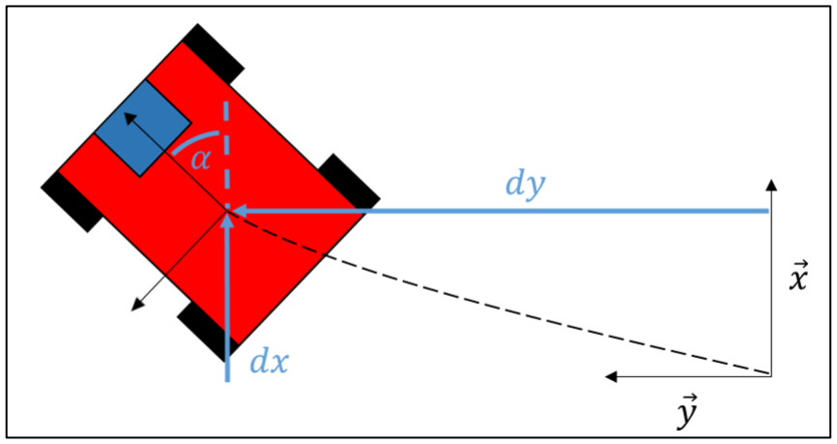
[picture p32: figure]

Figure 5: Odometry frame and variables

The displacement will be first expressed in the robot base frame:

- ω
- Δx
- Δy

And then added to the odometry frame using the following equations:

- α = α + ω
- dx = dx + Δx ∗ cos(α) − Δy ∗ sin(α)
- dy = dy + Δx ∗ sin(α) + Δy ∗ cos(α)

### 3.1 No angular speed

Without angular speed the odometry is very straight-forward:

- ω = 0
- Δx = dwf
- Δy = 0

### 3.2 With angular speed

Using the previous equations (1.2 Steering wheel with angle - page 3) the following equations are derived:

ω = d⏜wf ∗

cos(θ)
L

= d⏜wf ∗

sin(φ)
L

And

d⏜wr = d⏜wf cos(θ) tan(θ)

dwr

̇ = dwḟ cos(θ) tan(θ) + d⏜wf θ̇(cos(θ)(1 + tan
2
(θ)) − sin(θ) tan(θ))

dwr

̇ = dwḟ sin(θ) + d⏜wf θ̇(cos(θ) + sin(θ) tan(θ) − sin(θ) tan(θ))

dwr

̇ = dwḟ sin(θ) + d⏜wf θ̇cos(θ)

As before, Θ is considered constant. The odometry is computed from the front wheel displacement (d⏜wf) in a defined time period (Δt), the front wheel angle (φ) and displacement in the same defined time period. All that data is received from the motor controller board.

We can express the displacement and angle according to the data:

dwr

̇ = dwḟ sin( θ) = dwḟ cos(φ)

dwr = dwr

̇ ∗ Δt

ω = d⏜wf ∗

sin(φ)
L

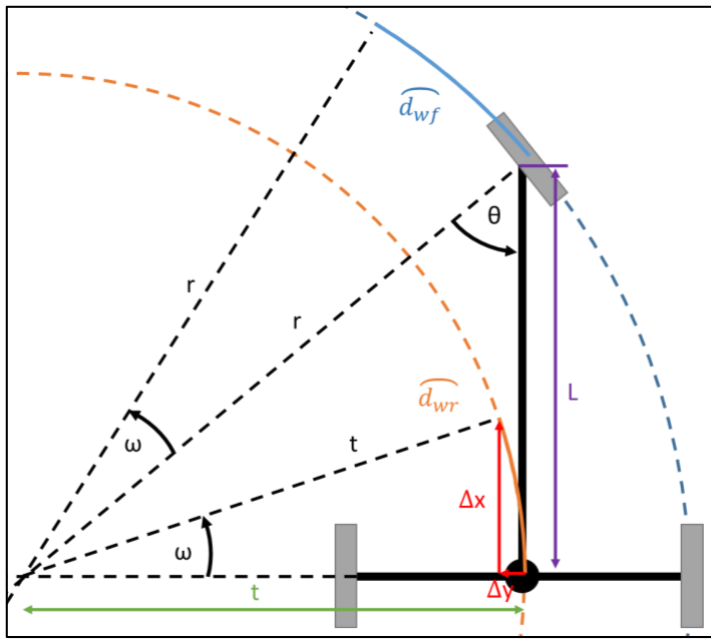
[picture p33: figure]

Figure 6: Displacement depending on front wheel angle and travelled distance

The odometry can then be deducted from the previous equations:

- ω = d⏜wf ∗

sin(φ)
L
- Δx = L tan(θ) sin(ω) = L cotan(φ) sin(ω) = L

cos(φ)
sin(φ)

sin(ω)

- Δy = t − t cos(ω) = t ∗ (1 − cos(ω)) = L

cos(φ)
sin(φ)

(1 − cos(ω))

## 4 Calibration

From odometry, some expressions can be derived to help with calibration.

The three variables to calibrate are:

- Front wheel angle offset
- Front wheel radius
- Robot’s length (distance between the kinematic center and the front wheel)

### 4.1 Front wheel angle calibration

The front wheel angle needs to be expressed relative to the other terms. Using again the equations from 3.2 - With angular speed page 7:

- d⏜wr = ω ∗ t
- Δx = L tan(θ) sin(ω) = L cotan(φ) sin(ω) = L

cos(φ)
sin(φ)

sin(ω)

- Δy = t − t cos(ω) = t ∗ (1 − cos(ω)) = L

cos(φ)
sin(φ)

(1 − cos(ω))

Δy = L

cos(φ)
sin(φ)

∗

sin(ω)
sin(ω)

∗ (1 − cos(ω)) =

Δx
sin(ω)

∗ (1 − cos(ω))

⇔

Δy
Δx

=

1 − cos(ω)
sin(ω)

= tan (

ω
2

)

⇔ ω = 2 ∗ arctan (

Δy
Δx

)

Moreover ω =

d⏜wr
t

d⏜wr
t

= 2 ∗ arctan (

Δy
Δx

)

t =

d⏜wr

2 ∗ arctan (

Δy
Δx

)

and t =

L
tan(φ)

⇔ tan(φ) = L ∗

2 ∗ arctan (

Δy
Δx

)

d⏜wr
⇔ φ = arctan(L ∗
2 ∗ arctan (

Δy
Δx

)

d⏜wr | )

### 4.2 Front wheel radius

The odometry gives the following equation:

traveled distance =

steps ∗ radiusfront wℎeel ∗ rms ∗ π 200

The odometry value can be corrected by simply adding a correcting factor:

real traveled distance =

steps ∗ factorcorrection ∗ radiusfront wℎeel ∗ rms ∗ π
200

This factor can be calculated by comparing the odometry value to the real value:

factorcorrection =

traveled distance
real traveled distance

### 4.3 Robot’s length

The following equation is given by the robot’s model:

d⏜wf = ω ∗ L ⇔ ω =

d⏜wf

L

The odometry value can be corrected by simply adding a correcting factor:

ωreal =

d⏜wf

L ∗ factorcorrection

This factor can be calculated by comparing the odometry value to the real value:

ωodometry

ωreal

=

d⏜wf

L

∗

L ∗ factorcorrection

d⏜wf

= factorcorrection

## Table of figures

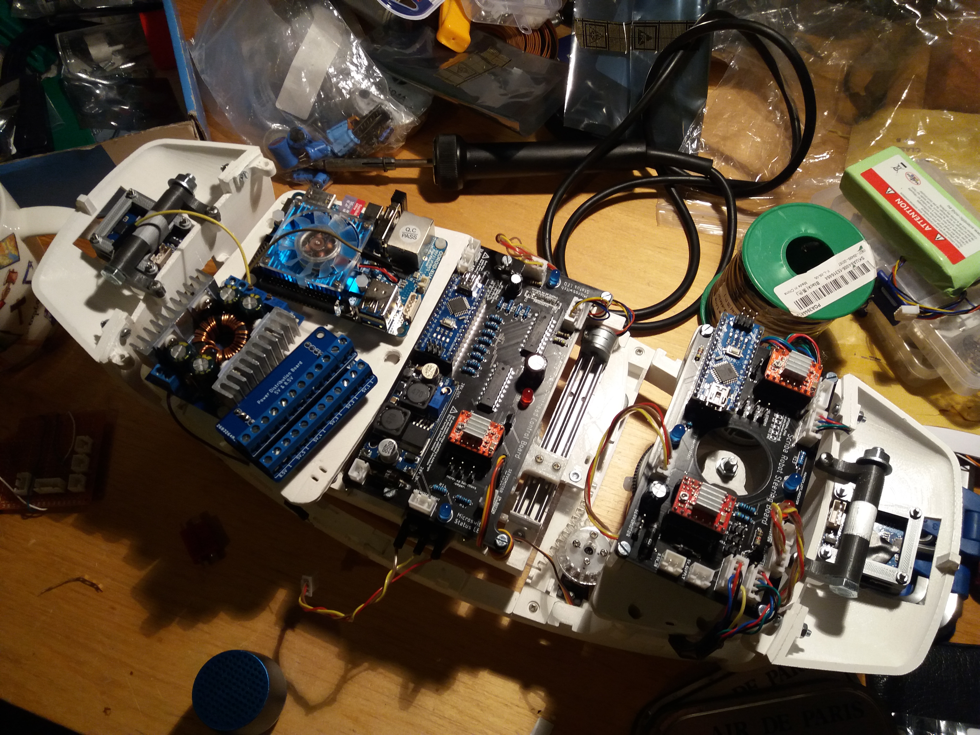
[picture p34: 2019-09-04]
Documentation/Pictures/Scriba3.jpg

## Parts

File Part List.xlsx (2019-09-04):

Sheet: 3D Printed Parts
Assembly Name | Part name | Qty | Accuracy Required? | Color | Printing Method | Status | Comment
Rear Assembly | Rear_base_support | 1 | Yes | White | FDM | Printed
Rear Assembly | Rear_battery_door | 1 | Yes | White | FDM | Printed | Rotation axle to sand
Rear Assembly | Slider_rotation_support_bottom | 1 | Yes | Doesn't matter | Resin | Not Printed
Rear Assembly | rear_board_support_bis | 1 | No | Doesn't matter | FDM | Ready For Printing
Rear Assembly | USB_hub_support | 1 | No | Doesn't matter | FDM | Printed
Rear Assembly | carter_rear | 1 | No | White | FDM | Printed
Camera Mount | camera_rotation_support_light (left) | 2 | No | White | FDM | Printed
Camera Mount | camera_rotation_support_light (right) | 2 | No | White | FDM | Printed
Camera Mount | camera_support_light | 2 | No | White | FDM | Printed
Camera Mount | led_ring_support | 6 | No | White | FDM | Printed
Camera Mount | slider_cam_support | 1 | No | White | FDM | Printed
Camera Mount | slider_cam_holder | 1 | No | White | FDM | Printed
Front Assembly | steer_motor_support_merged | 1 | No | Doesn't matter | FDM | Printed
Front Assembly | steer_roller_bearing_support | 1 | Yes | Doesn't matter | FDM | Printed
Front Assembly | microswitch_spacer_block | 1 | No | Doesn't matter | FDM | Not Printed
Front Assembly | steer_encoder_wheel_shaft | 1 | Yes | Doesn't matter | FDM | Not Printed
Steering Wheel | Front_wheel_support | 1 | No | Doesn't matter | FDM | Printed
Steering Wheel | Front_wheel_shaft | 1 | Yes | Doesn't matter | FDM | Not Printed
Steering Wheel | end_position_steering_shaft | 1 | No | Doesn't matter | FDM | Printed
Slider Assembly | slider_rotation_axle | 1 | Yes | Doesn't matter | FDM | Printed
Slider Assembly | prinhead_slider | 1 | Yes | Doesn't matter | FDM | Printed
Slider Assembly | slider_support_rotation_gear | 1 | Yes | Doesn't matter | Resin | Not Printed | Plexiglass Laser cut?
Carter & Frame | carter_surface_cut_1 | 1 | No | Black | FDM | Ready For Printing
Carter & Frame | carter_surface_cut_2 | 1 | No | Black | FDM | Ready For Printing
Carter & Frame | carter_front | 1 | Yes | White | FDM | Ready For Printing
Carter & Frame | carter_side_left_cut_1 | 1 | No | Black | FDM | Printed | Increase nut hole size for easier support removal
Carter & Frame | carter_side_left_cut_2 | 1 | No | Black | FDM | Printed | Increase nut hole size for easier support removal
Carter & Frame | carter_side_right_cut_1 | 1 | No | Black | FDM | Printed | Increase nut hole size for easier support removal
Carter & Frame | carter_side_right_cut_2 | 1 | No | Black | FDM | Printed | Increase nut hole size for easier support removal
Carter & Frame | carter_cam | 2 | No | White | FDM | Printed
Carter & Frame | frame_side_left_cut_1 | 1 | No | Doesn't matter | FDM | Not Printed | TO BE REDO
Carter & Frame | frame_side_left_cut_2 | 1 | No | Doesn't matter | FDM | Printed | Size to be adapted is slider rotation gear laser cut in plexiglas
Carter & Frame | frame_side_right_cut_1 | 1 | No | Doesn't matter | FDM | Printed | Size to be adapted is slider rotation gear laser cut in plexiglas
Carter & Frame | frame_side_right_cut_2 | 1 | No | Doesn't matter | FDM | Printed | Size to be adapted is slider rotation gear laser cut in plexiglas
Carter & Frame | Servo gear 0.7M 35T | 1 | Yes | Doesn't matter | Resin | Printed
Carter & Frame | front_support | 1 | No | Doesn't matter | FDM | Not Printed | Size to be adapted is slider rotation gear laser cut in plexiglas

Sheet: Sensors, Actuators & Electronic
Categories | Component | Qty | Reference | Datasheet | Part(s) Name(s) (in CAD) | Supplier | Status
Motor | Traction Stepper Motor | 1 | 14HR08-0654S | https://www.omc-stepperonline.com/round-nema-14-bipolar-09deg-85ncm-12ozin-065a-46v-%CF%8636x20mm-4-wires-14hr08-0654s.html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 | round_nema_14_long | Stepper Online | Delivered
Motor | Steering Stepper Motor | 1 | 14HR05-0504S | https://www.omc-stepperonline.com/round-nema-14-bipolar-09deg-5ncm-708ozin-05a-85v-%CF%8636x12mm-4-wires-14hr05-0504s.html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 | round_nema_14_short | Stepper Online | Delivered
Camera | ELP Camera 2.1mm Lens | 1 | ELP-USBFHD01M-L21 | https://fr.aliexpress.com/item/32261191143.html?spm=a2g0s.12269583.0.0.34497ae2zEOrfk | elp-cam | AliExpress | Delivered
Camera | ELP Camera 2.8mm Lens | 2 | ELP-USBFHD01M-L28 | https://fr.aliexpress.com/item/32261191143.html?spm=a2g0s.12269583.0.0.34497ae2zEOrfk | elp-cam | AliExpress | Delivered
Sensor | Encoder 5V Freescale | 2 |  | https://fr.aliexpress.com/item/32643642446.html?spm=a2g0s.9042311.0.0.6eb66c37Qs25wK | encoder | AliExpress | Delivered
 |  |  |  |  | encoder_wheel |  | Delivered
Sensor | Microswitch | 4 | KW12-3 Micro Limit Switch Roller Lever 5A 125V Open/Close Switch | https://www.banggood.com/10Pcs-Micro-Limit-Switch-Roller-Lever-5A-125V-Open-Close-Switch-p-945733.html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 | microswitch | Banggood | Delivered
Motor | EMAX ES09MD Servomotor | 1 | EMAX ES09MD servo | https://www.banggood.com/EMAX-ES09MD-Digital-Swash-Servo-For-450-Helicopter-With-Metal-Gear-p-88192.html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 | EMAX_ES09MD_Servo | Banggood | Delivered
 |  |  |  |  | servo_horn |  | Delivered
Motor | Printhead Stepper Motor | 1 | DC 4-9V Drive Stepper Motor Screw With Nut Slider 2 Phase 4 Wire | https://www.banggood.com/DC-4-9V-Drive-Stepper-Motor-Screw-With-Nut-Slider-2-Phase-4-Wire-p-964613.html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 | slider_motor | Banggood | Delivered
Control Board | Arduino Nano | 2 | Geekcreit® ATmega328P Nano V3 Module | https://www.banggood.com/Geekcreit-ATmega328P-Nano-V3-Module-Improved-Version-With-USB-Cable-Development-Board-For-Arduino-p-933647.html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 | User Library-arduino_nano | Banggood | Delivered
Control Board | Odroid-XU4 | 1 | G143452239825 | https://magazine.odroid.com/wp-content/uploads/odroid-xu4-user-manual.pdf | Odroid XU4 | HardKernel | Delivered
Control Board | Odroid Shifter Shield | 1 | G143556253995 | https://www.hardkernel.com/shop/xu4-shifter-shield/ | Odroid XU4 Shifter Shield | HardKernel | Delivered
Control Board | A4988 Stepper Driver | 3 | Geekcreit® 3D Printer A4988 Reprap Stepping Stepper Step Motor Driver Module | https://www.banggood.com/3D-Printer-A4988-Reprap-Stepping-Stepper-Step-Motor-Driver-Module-p-88765.html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 | User Library-A4988 | Banggood | Delivered
Power Board | 5V Step-up/down Module | 1 | SH-PWS14 | https://www.dx.com/p/dc-5-30v-to-dc-1-25-30v-adjustable-step-up-step-down-constant-voltage-constant-current-module-2060596 | SH-PWS14_DC-DC_Converter | Dealextreme | Delivered
Power Board | 8.5V/20V Step-up/down Module | 2 | XL6009 | https://www.banggood.com/3pcs-DC-DC-Boost-Buck-Adjustable-Step-Up-Step-Down-Automatic-Converter-XL6009-Module-p-1087604.html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 | stepdown voltage converter | Banggood | Delivered
Display | Li-po Battery Indicator Display Board | 1 | Li-po Battery Indicator Display Board Power Storage Monitor - 3S | https://www.banggood.com/3_7V7_4V-11_1V14_8V-Li-po-Battery-Indicator-Display-Board-Power-Storage-Monitor-p-1096280.html?ID=47892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 | battery_indicator | Banggood | Delivered
Battery | Black Lithium 11.1V 1500mAh | 1 | Z03L9150330 |  | battery | Protronik (Jet Modélisme Lyon) | Delivered
Light | 8 RGB Led Ring | 3 | 8 Round Shape WS2812B SMD5050 RGBW RGBWW 4 In 1 LED Light Chip Board DC5V | https://www.banggood.com/1PC-8PCS-12PCS-16PCS-24PCS-Round-Shape-WS2812B-SMD5050-RGBW-RGBWW-4-In-1-LED-Light-Chip-Board-DC5V-p-1202247.html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 | rgb_led_ring_x8 | Banggood | Delivered
 |  |  |  | https://learn.adafruit.com/adafruit-neopixel-uberguide/basic-connections |  |  | Delivered
Printhead | HP 51604A Printhead | 1 | HP 51604A |  | HP_51604A_printhead |  | Delivered

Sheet: Electronic Components
Assembly or Board Name | Component Name | Qty | Reference | Datasheet | Status | Concegrated List
Low Voltage Disconnect Board | Relay SONGLE Mini 12V DC | 1 | SRD-12VDC-SL-C | https://www.banggood.com/5Pcs-SONGLE-Mini-12V-DC-Power-Relay-SRD-12VDC-SL-C-PCB-Type-p-955021.html | Not Ordered | Étiquettes de lignes | Quantity | Status
Low Voltage Disconnect Board | CMOS Quad 2-Input NOR Gate | 1 | CD4001B | http://www.ti.com/product/CD4001B | Not Ordered | 15 Pins Female Header 0.1" | 4 | Delivered
Low Voltage Disconnect Board | Resistor 1K | 1 |  |  | Not Ordered | 2 Pins Female Header 0.1" | 9 | Delivered | 9
Low Voltage Disconnect Board | Resistor 4,7K | 1 |  |  | Not Ordered | 2 Pins Male Header 0.1" | 9 | Delivered | 9
Low Voltage Disconnect Board | Resistor 100K | 1 |  |  | Not Ordered | 3 Pins Male Header 0.1" | 1 | Delivered
Low Voltage Disconnect Board | Resistor 24.9K | 1 |  |  | Not Ordered | 5 Pins Female Header 0.1" | 2 | Delivered
Low Voltage Disconnect Board | Resistor 220K | 1 |  |  | Not Ordered | 5 Pins Male Header 0.1" | 2 | Delivered
Low Voltage Disconnect Board | Resistor 10Meg | 1 |  |  | Not Ordered | 8 Pins Female Header 0.1" | 6 | Delivered | 6
Low Voltage Disconnect Board | Potentiometer 250K | 1 |  | https://www.banggood.com/10-Value-100pcs-1001M-Trimmer-Resistor-Trim-Pot-Potentiometer-Kit-p-1071345.html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 | Not Ordered | Capacitor 100µF | 2 | Delivered
Low Voltage Disconnect Board | Diode 1N914 | 1 |  |  | Not Ordered | Capacitor 1000µF | 3 | Delivered | 3
Low Voltage Disconnect Board | Capacitor 470nF | 1 |  |  | Not Ordered | Capacitor 10nF | 1 | Delivered | non ploarized
Low Voltage Disconnect Board | Capacitor 10nF | 1 |  |  | Not Ordered | Capacitor 220µF | 1 | Delivered | 20V min
Low Voltage Disconnect Board | TLV431x Low-Voltage Adjustable Precision Shunt Regulator | 1 | TLV431 | http://www.ti.com/lit/ds/symlink/tlv431.pdf | Not Ordered | Capacitor 470nF | 1 | Delivered
Low Voltage Disconnect Board | Led Button | 1 |  | https://www.banggood.com/5Pcs-Blue-LED-Power-Symbol-Momentary-Latching-Switch-LED-Light-Push-Button-SPST-p-1066920.html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 | Delivered | CMOS Quad 2-Input NOR Gate | 1 | Ordered
Low Voltage Disconnect Board | JST Connector 2 Pins | 3 |  |  | Not Ordered | Deans Connector | 1 | Ordered
Low Voltage Disconnect Board | Deans Connector | 1 |  | https://www.banggood.com/Excellway-DC-012-20pcs-T-Plug-Male-Female-Connectors-Deans-Style-For-RC-LiPo-Battery-p-1304841.html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 | Not Ordered | Diode 1N4933 | 2 | Delivered | PX1N4003, 1N4004 ou 1N4007 en remplacement
Low Voltage Disconnect Board | LVD Board | 1 |  |  | Not Ordered | Diode 1N914 | 1 | Delivered | PX1N4003, 1N4004 ou 1N4007 en remplacement
Power Distribution Board | Power Distribution Board Bottom | 1 |  |  | Not Ordered | Diode DO15 (>3A, A DETERMINER) | 3 | Delivered
Power Distribution Board | Power Distribution Board Top | 1 |  |  | Not Ordered | JST Connector 2 Pins | 10 | Delivered
Power Distribution Board | Terminal Block 2 Pins | 12 |  | https://www.banggood.com/60pcs-2-Pin-Plug-In-Screw-Terminal-Block-Connector-5_08mm-Pitch-p-1185450.html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 | Delivered | JST Connector 3 Pins | 4 | Delivered | 2
Power Distribution Board | JST Connector 2 Pins | 2 |  |  | Not Ordered | JST Connector 4 Pins | 5 | Delivered
Power Distribution Board | 5 Pins Female Header 0.1" | 2 |  |  | Delivered | Led (Blue) | 4 | Delivered
Power Distribution Board | 5 Pins Male Header 0.1" | 2 |  |  | Delivered | Led Button | 1 | Delivered
Printhead Control Board | ULN2803 Darlington Array | 2 | ULN2803 | https://www.sparkfun.com/datasheets/IC/uln2803a.pdf | Delivered | LVD Board | 1 | Not Ordered
Printhead Control Board | Resistor 1K | 12 |  |  |  | Potentiometer 250K | 1 | Ordered
Printhead Control Board | Resistor 100 | 2 |  |  |  | Power Distribution Board Bottom | 1 | Not Ordered
Printhead Control Board | Diode 1N4933 | 1 |  |  |  | Power Distribution Board Top | 1 | Not Ordered
Printhead Control Board | Diode DO15 (>3A, A DETERMINER) | 2 |  |  |  | Printhead Contact Board | 1 | Not Ordered
Printhead Control Board | JST Connector 2 Pins | 3 |  |  |  | Printhead Control Board | 1 | Not Ordered
Printhead Control Board | JST Connector 3 Pins | 2 |  |  |  | Relay SONGLE Mini 12V DC | 1 | Ordered
Printhead Control Board | JST Connector 4 Pins | 1 |  |  |  | Resistor 100 | 4 | Delivered
Printhead Control Board | Capacitor 220µF | 1 |  |  |  | Resistor 100K | 1 | Delivered
Printhead Control Board | Capacitor 100µF | 1 |  |  |  | Resistor 10Meg | 1 | Ordered
Printhead Control Board | Led (Blue) | 2 |  | https://www.banggood.com/100pcs-20Ma-F5-5MM-5Colors-Ultra-Bright-LED-Diode-p-966103.html?rmmds=myorder | Delivered | Resistor 1K | 13 | Delivered
Printhead Control Board | 8 Pins Female Header 0.1" | 2 |  |  |  | Resistor 220K | 1 | Delivered
Printhead Control Board | 15 Pins Female Header 0.1" | 2 |  |  |  | Resistor 24.9K | 1 | Delivered | 24k
Printhead Control Board | 2 Pins Female Header 0.1" | 3 |  |  |  | Resistor 4,7K | 1 | Delivered
Printhead Control Board | 2 Pins Male Header 0.1" | 3 |  |  |  | Steering Board | 1 | Not Ordered
Printhead Control Board | Printhead Control Board | 1 |  |  | Not Ordered | Terminal Block 2 Pins | 12 | Delivered
Printhead Contact Board | Printhead Contact Board | 1 |  |  | Not Ordered | TLV431x Low-Voltage Adjustable Precision Shunt Regulator | 1 | Ordered | Verifier montage sur EAGLE
Steering Board | Resistor 100 | 2 |  |  |  | ULN2803 Darlington Array | 2 | Delivered
Steering Board | Diode 1N4933 | 1 |  |  |  | Total général | 118
Steering Board | Diode DO15 (>3A, A DETERMINER) | 1
Steering Board | JST Connector 2 Pins | 2
Steering Board | JST Connector 3 Pins | 2
Steering Board | JST Connector 4 Pins | 4
Steering Board | Capacitor 100µF | 1
Steering Board | Led (Blue) | 2 |  | https://www.banggood.com/100pcs-20Ma-F5-5MM-5Colors-Ultra-Bright-LED-Diode-p-966103.html?rmmds=myorder | Delivered
Steering Board | 8 Pins Female Header 0.1" | 4
Steering Board | 15 Pins Female Header 0.1" | 2
Steering Board | 2 Pins Female Header 0.1" | 6
Steering Board | 2 Pins Male Header 0.1" | 6
Steering Board | 3 Pins Male Header 0.1" | 1
Steering Board | Steering Board | 1 |  |  | Not Ordered
Led Rings | Capacitor 1000µF | 3
Led Rings | Resistor 470ohm | 3 |  |  | Delivered

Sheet: Screws, Bolts, Gears & More
Assembly Name | Component | Qty | Reference | Datasheet | Status | Congregated List
Camera Mount | Screw M2x16 | 8 |  |  | Not Ordered | Component | Quantity | Status
Camera Mount | Nut M2 | 8 |  |  | Not Ordered | Ball Bearing 4x13x5 | 4 | Delivered
Camera Mount | Screw M1.5 ? | 4 |  |  |  | Ball Bearing Flanged 3x8x4 | 4 | Delivered
Camera Mount | Screw M6x60 | 2 |  |  | Not Ordered | Nut M2 | 22 | Not Ordered | 20
Camera Mount | Washer M6 | 2 |  |  | Not Ordered | Nut M3 | 28 | Delivered | 29
Camera Mount | Nut M6 | 2 |  |  | Not Ordered | Nut M4 | 3 | Delivered
Camera Mount | Wood Screw M3 | 4 |  |  |  | Nut M6 | 2 | Delivered
Rear Assembly | Threaded Rod M3 | 1 |  |  | Not Ordered | Screw M1.5 ? | 4 | Not Ordered
Rear Assembly | Nut M3 | 8 |  |  | Not Ordered | Screw M2 (Cut Short) | 3 | Delivered | M3x10 to cut
Rear Assembly | Washer M3 | 2 |  |  | Not Ordered | Screw M2x16 | 18 | Not Ordered
Rear Assembly | Ball Bearing Flanged 3x8x4 | 4 |  | https://www.banggood.com/10pcs-F693ZZ-3mmx8mmx4mm-Double-Shielded-Flanged-Ball-Bearings-p-1096089.html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 | Delivered | Screw M2x20 | 2 | Not Ordered
Rear Assembly | Screw M4x30 | 1 |  |  | Not Ordered | Screw M2x8 | 4 | Delivered
Rear Assembly | Nut M4 | 2 |  |  | Not Ordered | Screw M3x10 | 30 | Delivered | 29
Rear Assembly | Ball Bearing 4x13x5 | 2 |  |  | Delivered | Screw M3x12 | 1 | Not Ordered
Rear Assembly | Wood Screw M3 | 6 |  |  |  | Screw M3x20 | 1 | Not Ordered
Rear Assembly | Wood Screw M2 | 6 |  |  |  | Screw M3x5 | 12 | Not Ordered | 7
Rear Assembly | Screw M3x5 | 12 |  |  |  | Screw M4x30 | 1 | Delivered
Rear Assembly | Screw M3x10 | 2 |  |  |  | Screw M4x40 | 1 | Not Ordered
Rear Assembly | Spacer L5 | 13 |  |  |  | Screw M6x60 | 2 | Delivered
Rear Assembly | Wood Screw M2x8 | 1 |  |  |  | Slider Shaft | 2 | Delivered
Rear Assembly | Wood Screw M1x8 | 1 |  |  |  | Spacer L15 | 8 | Delivered
Slider Assembly | Wood Screw M2x8 | 14 |  |  |  | Spacer L5 | 13 | Delivered
Slider Assembly | Wood Screw M2x10 | 2 |  |  |  | Threaded Rod M3 | 1 | Delivered
Slider Assembly | Screw M2x16 | 8 |  |  |  | Washer M3 | 6 | Delivered
Slider Assembly | Nut M2 | 10 |  |  |  | Washer M6 | 2 | Delivered
Slider Assembly | Screw M3x10 | 6 |  |  |  | Wood Screw M1.6 | 4 | Not Ordered
Slider Assembly | Nut M3 | 4 |  |  |  | Wood Screw M1x8 | 1 | Not Ordered
Slider Assembly | Screw M2x8 | 4 |  |  |  | Wood Screw M2 or M1.6 | 3 | Not Ordered
Slider Assembly | Screw M3x12 | 4 |  |  |  | Wood Screw M2x10 | 2 | Not Ordered
Slider Assembly | Screw M3x20 | 1 |  |  |  | Wood Screw M2x8 | 15 | Not Ordered
Slider Assembly | Washer M3 | 2 |  |  |  | Wood Screw M3 | 23 | Delivered | 22
Slider Assembly | Slider Shaft | 2 |  |  |  | Wood Screw M2 | 6 | Not Ordered
Slider Assembly | Spacer L15 | 4 |  |  |  | Roller Ball | 1 | Ordered
Frame & Carter | Roller Ball | 1 |  |  |  | Total | 229
Frame & Carter | Wood Screw M3 | 4
Frame & Carter | Wood Screw M1.6 | 4
Frame & Carter | Screw M3x10 | 12
Frame & Carter | Nut M3 | 12
Steering Motor Assembly | Screw M2 (Cut Short) | 2
Steering Motor Assembly | Screw M3x10 | 6
Steering Motor Assembly | Nut M3 | 2
Steering Motor Assembly | Washer M3 | 2
Steering Motor Assembly | Screw M2x16 | 2
Steering Motor Assembly | Screw M2x20 | 2
Steering Motor Assembly | Nut M2 | 4
Steering Motor Assembly | Wood Screw M3 | 8
Steering Motor Assembly | Spacer L15 | 4
Steering Motor Assembly | Ball Bearing 4x13x5 | 2 |  |  | Delivered
Steering Wheel Assembly | Screw M4x40 | 1
Steering Wheel Assembly | Nut M4 | 1
Steering Wheel Assembly | Screw M3x10 | 4
Steering Wheel Assembly | Nut M3 | 2
Steering Wheel Assembly | Wood Screw M3 | 1
Steering Wheel Assembly | Screw M2 (Cut Short) | 1
Steering Wheel Assembly | Wood Screw M2 or M1.6 | 3

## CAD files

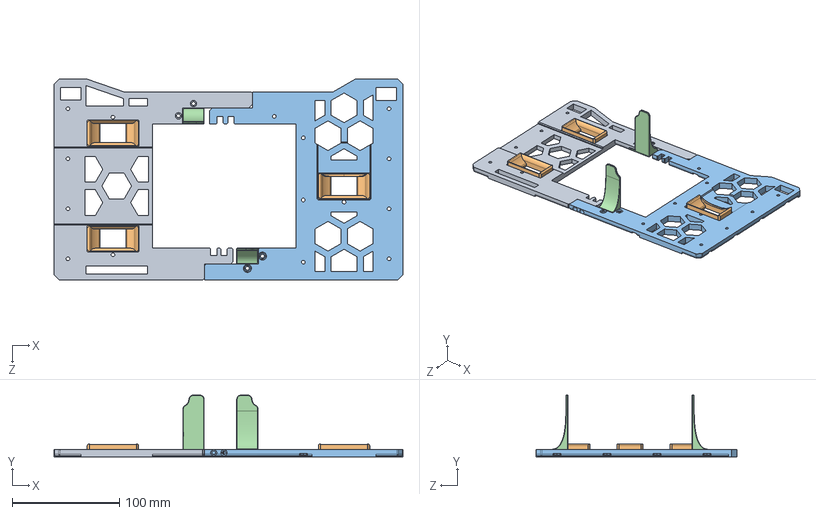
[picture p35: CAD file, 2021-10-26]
CAD/calibration_tool/calibration_rig.SLDASM
325.6 x 57.7 x 187.9 mm
rear
wheel_block x 3
front
slider_support_block_reversed x 2

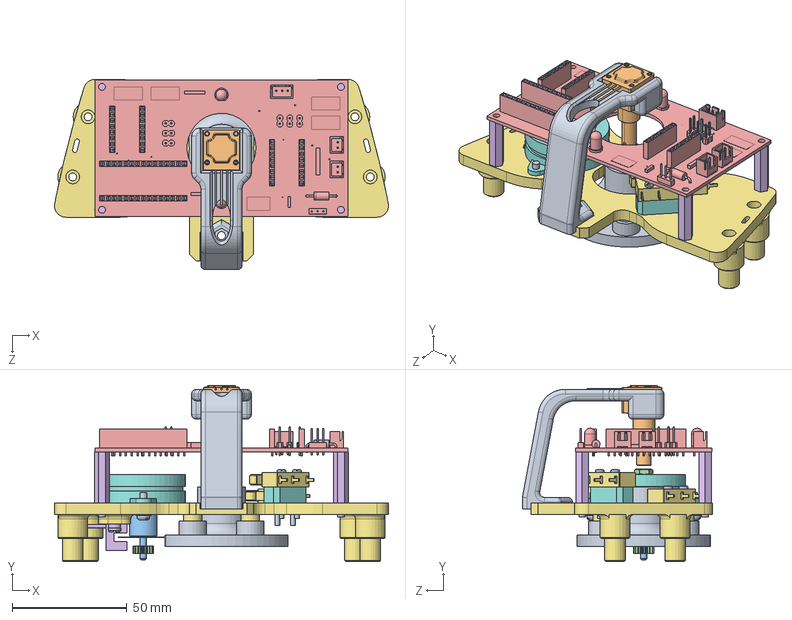
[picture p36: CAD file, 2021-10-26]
CAD/front_assembly/front_assembly.SLDASM
145.4 x 76.7 x 82.8 mm
steer_roller_bearing_support
radial ball bearing_68_iso x 2
pan head cross recess screw_iso x 4
hex thin nut chamfered gradeab_iso x 7
Steering_board
spacer_M6_L15 x 4
steer_motor_support_merged
round_nema_14_short
slotted pan head screw_iso x 8
plain washer normal grade a_iso x 2
steer_encoder_wheel_shaft
spur gear_iso
encoder_wheel
encoder
microswitch x 2
microswitch_spacer_block
steering_pot_holder
91A1A-B28.stp

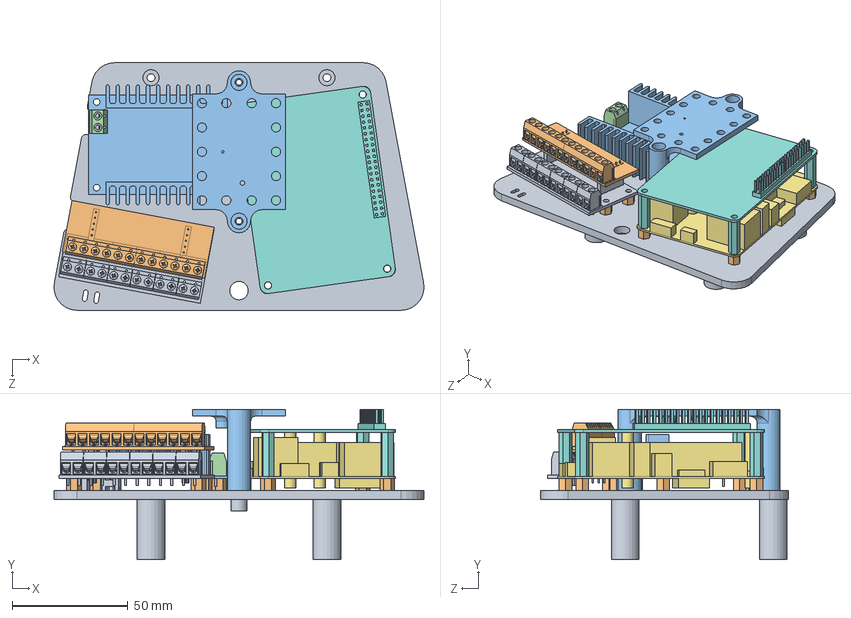
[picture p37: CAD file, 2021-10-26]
CAD/rear_assembly/rear_board_assembly/read_board_assembly.SLDASM
159.9 x 65.0 x 107.0 mm
rear_board_support_bis
spacer_M6_L5 x 10
SH-PWS14_DC-DC_Converter
ScrewTerminalCover x 2
Pin x 4
Odroid XU4
Odroid XU4 Shifter Shield
power_distribution_board_bottom
power_distribution_board_top
USB_hub_support

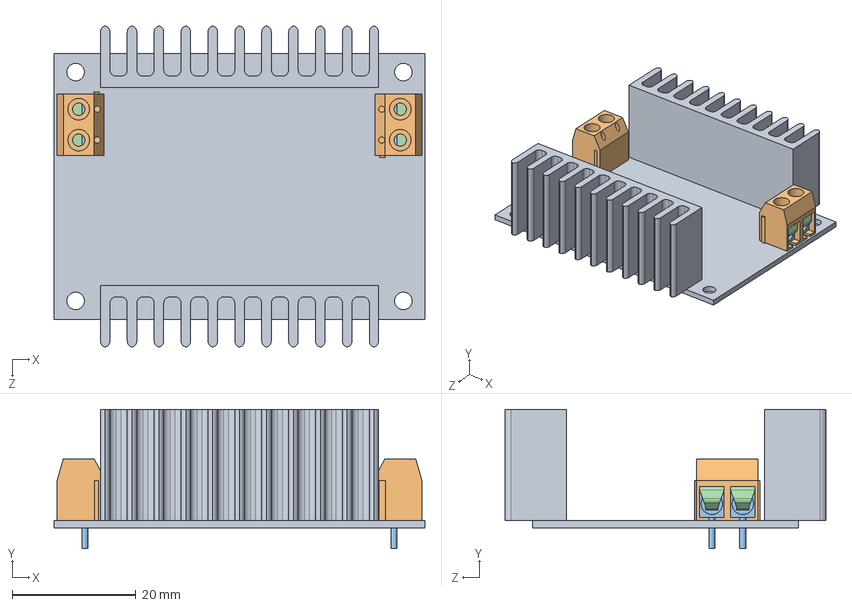
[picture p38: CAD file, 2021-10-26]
CAD/rear_assembly/rear_board_assembly/SH-PWS14_DC-DC_Converter_5V/SH-PWS14_DC-DC_Converter_5V.SLDASM
60.0 x 22.5 x 51.9 mm
SH-PWS14_DC-DC_Converter
ScrewTerminalCover x 2
Pin x 4

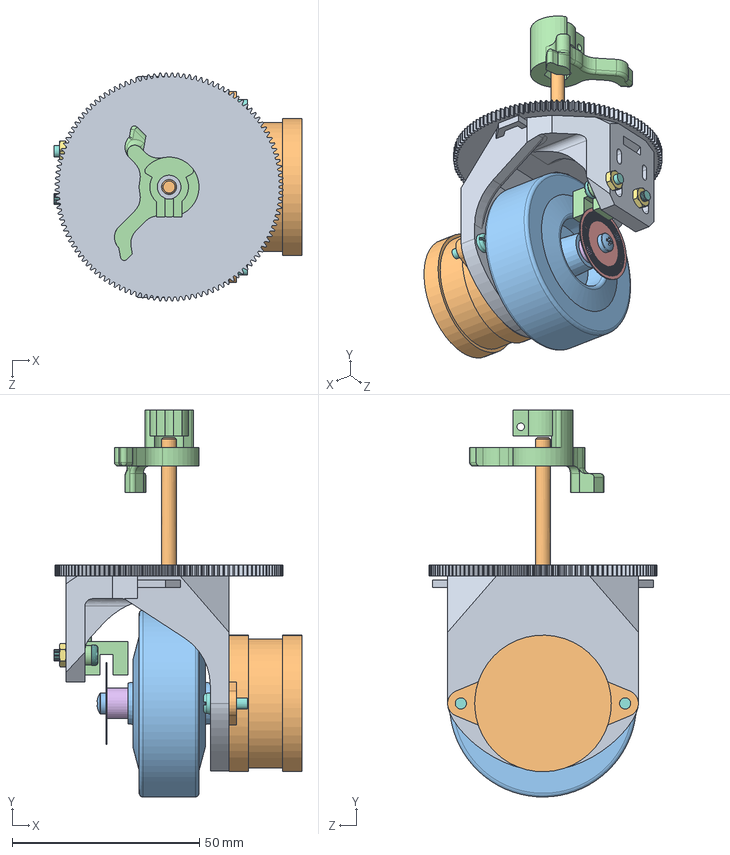
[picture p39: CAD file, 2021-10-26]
CAD/steering_wheel/steering_wheel.SLDASM
66.2 x 103.4 x 61.0 mm
front_wheel_support
round_nema_14_long
wheel
encoder
encoder_wheel
front_wheel_shaft
hex thin nut chamfered gradeab_iso x 2
slotted pan head screw_iso x 5
spur gear_iso
hex bolt gradeab_iso
pan head cross recess screw_iso
end_position_steering_shaft

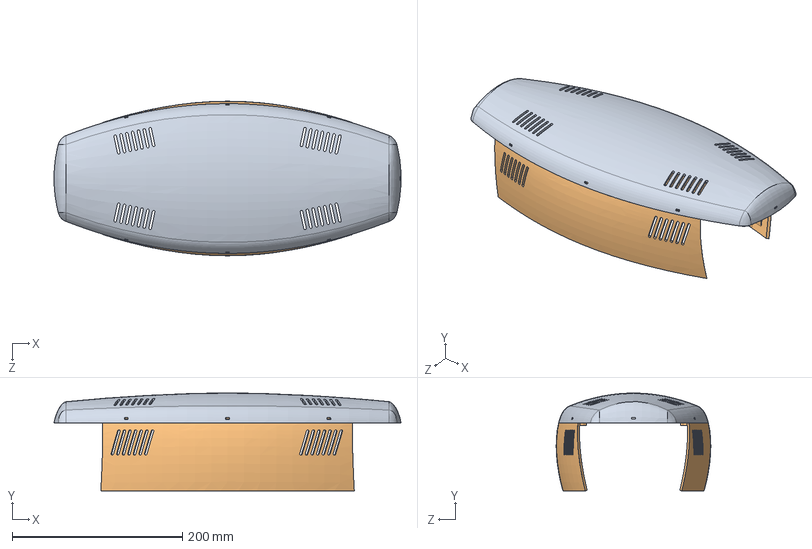
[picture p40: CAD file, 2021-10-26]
CAD/carter_assembly/carter_assembly.SLDASM
407.8 x 115.0 x 181.7 mm
carter_surface
carter_side x 2

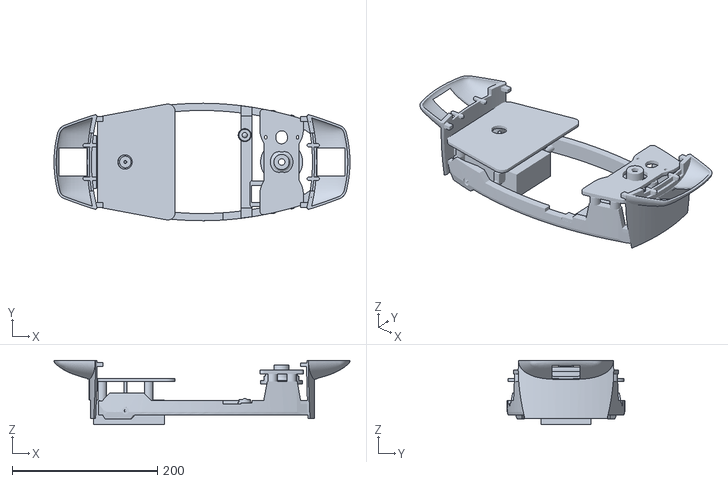
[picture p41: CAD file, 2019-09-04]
Code/ROS/scriba_description/meshes/main_body.STL
408.0 x 162.0 x 88.3

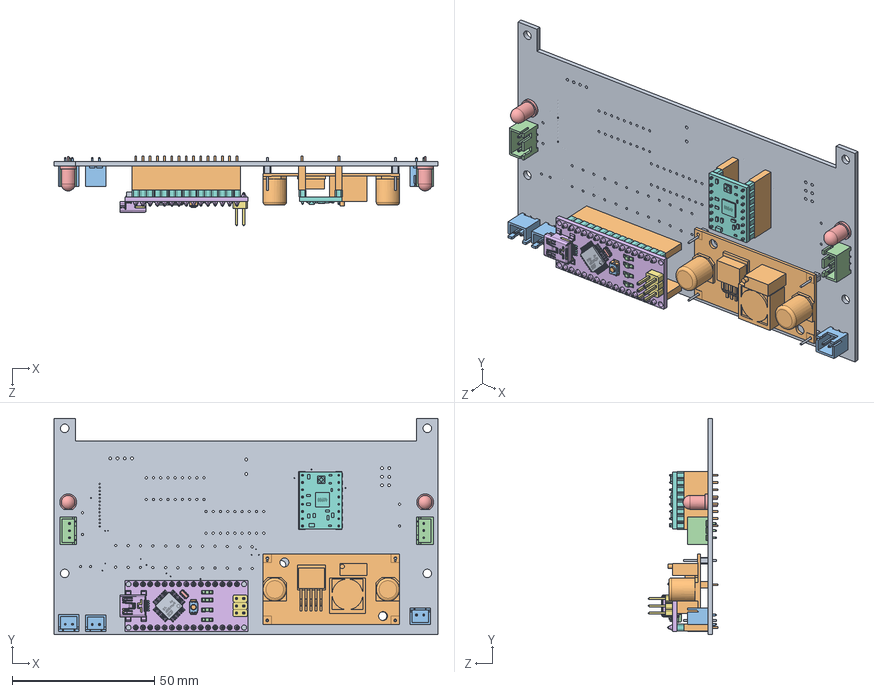
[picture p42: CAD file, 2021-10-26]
CAD/slider_assembly/printhead_control_board/Printhead_control_board.sldasm
135.0 x 76.0 x 24.5 mm
Printhead_control_board
2.54_pin_female_headers x 4
JST - XH - Thru - 2Pin - 2.5mm (Genuine) x 3
JST - XH - Thru - 3Pin - 2.5mm (Genuine) x 2
LED 5mm light blue TH x 2
User Library-arduino_nano_nano-board
User Library-arduino_nano_2pin_header__02 x 3
User Library-arduino_nano_15pin_header__ x 2
User Library-arduino_nano_atmega328
User Library-arduino_nano_ftdi FT232rl
User Library-arduino_nano_smt_resistor222 x 5
User Library-arduino_nano_led x 4
User Library-arduino_nano_16mhz crystal - measured
User Library-arduino_nano_MINIUSBSHELL
User Library-arduino_nano_MINIUSBCORE
User Library-arduino_nano_MINI USB CONTACT x 5
User Library-arduino_nano_cap106C x 2
User Library-arduino_nano_reset core
User Library-arduino_nano_reset shell
User Library-arduino_nano_nano - reg
User Library-arduino_nano_NANO DIODE
User Library-arduino_nano_189 RESISTOR PACK
User Library-arduino_nano_102 RESISTOR PACK
User Library-A4988
2.54_pin_male_headers x 4
stepdown voltage converter

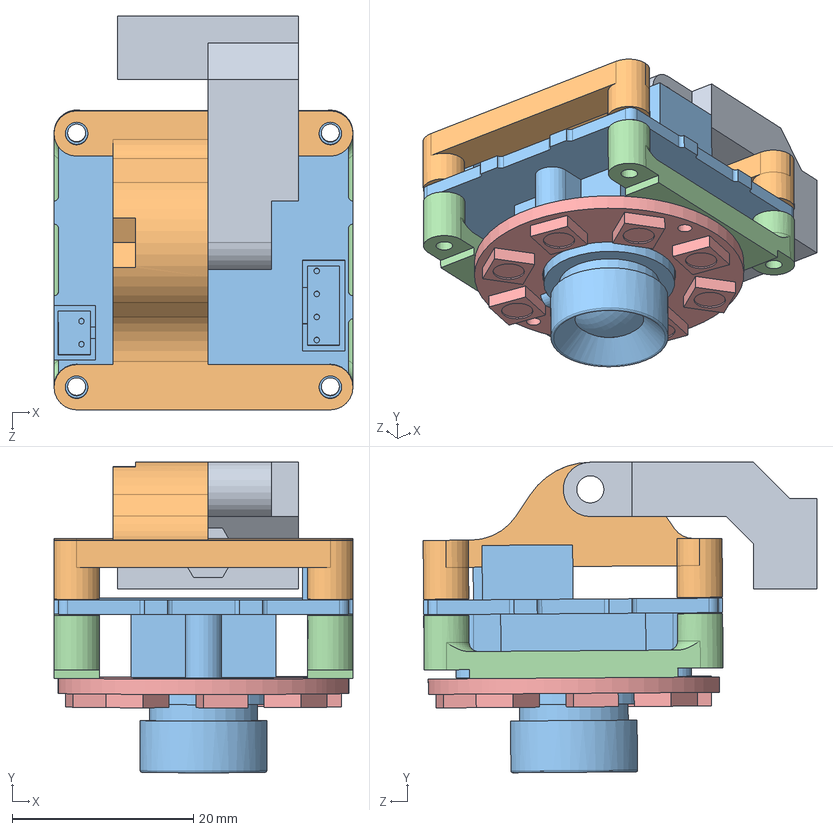
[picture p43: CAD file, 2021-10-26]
CAD/slider_assembly/slider_cam_assembly/slider_cam_assembly.SLDASM
33.0 x 34.3 x 43.5 mm
slider_cam_holder
slider_cam_support
elp-cam
led_ring_support x 2
rgb_led_ring_x8

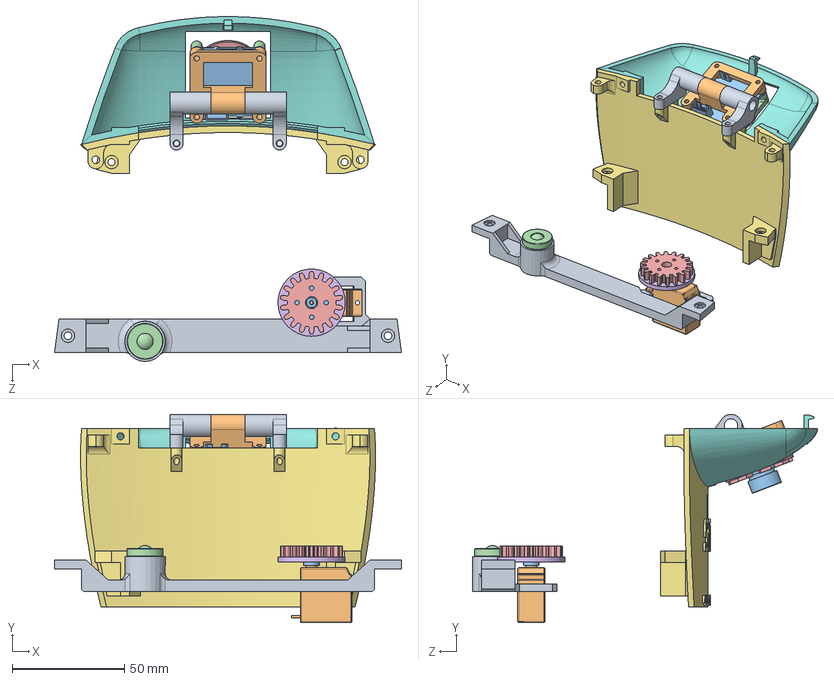
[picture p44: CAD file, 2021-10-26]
CAD/frame_assembly/frame_assembly.SLDASM
154.9 x 92.9 x 154.0 mm
front_support
EMAX_ES09MD_Servo
servo_horn
Ball_Conveyor_Roller_CY-8H
Involute_gear_small
gear_support
carter_front
carter_cam
camera_rotation_support_light x 2
camera_support_light
elp-cam
led_ring_support x 2
rgb_led_ring_x8

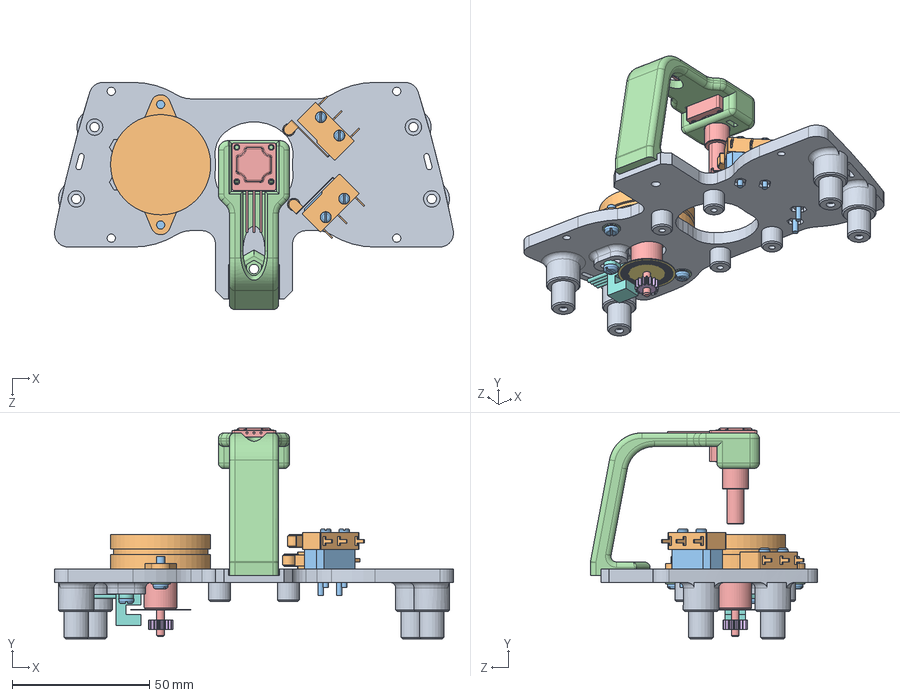
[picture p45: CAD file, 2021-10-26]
CAD/front_assembly/steering_motor_assembly/steering_motor_assembly_merged.SLDASM
145.4 x 76.7 x 82.8 mm
steer_motor_support_merged
round_nema_14_short
slotted pan head screw_iso x 8
plain washer normal grade a_iso x 2
steer_encoder_wheel_shaft
spur gear_iso
encoder_wheel
encoder
hex thin nut chamfered gradeab_iso x 6
microswitch x 2
microswitch_spacer_block
steering_pot_holder
91A1A-B28.stp

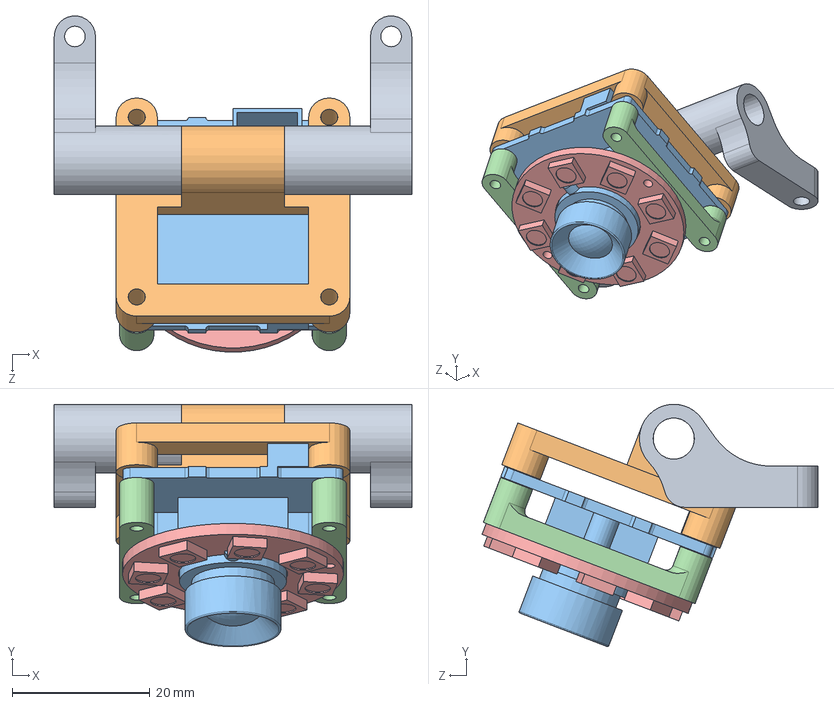
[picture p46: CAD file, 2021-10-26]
CAD/cam_assembly/cam_mount_light.SLDASM
52.0 x 35.2 x 48.9 mm
camera_rotation_support_light x 2
camera_support_light
elp-cam
led_ring_support x 2
rgb_led_ring_x8

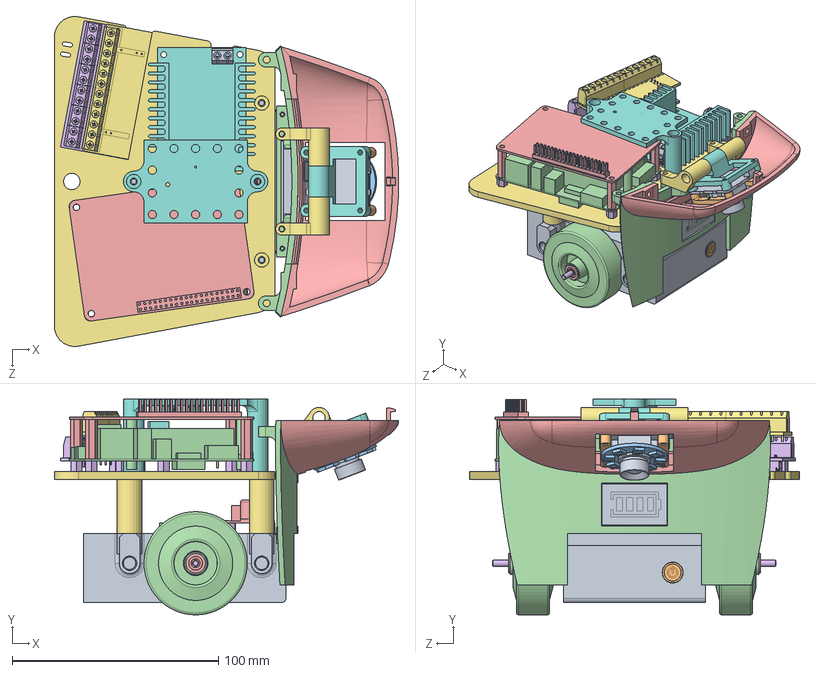
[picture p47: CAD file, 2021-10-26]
CAD/rear_assembly/rear_assembly_2.SLDASM
166.9 x 104.5 x 159.9 mm
Rear_base_support
battery
rear_battery_door
wheel x 2
stepdown voltage converter
spacer_M6_L5 x 12
camera_rotation_support_light x 2
camera_support_light
elp-cam
led_ring_support x 2
rgb_led_ring_x8
slider_rotation_support_bottom
ball_bearing_flanged_3x8x4 x 4
threaded_rod_M3 x 2
rear_board_support_bis
SH-PWS14_DC-DC_Converter
ScrewTerminalCover x 2
Pin x 4
Odroid XU4
Odroid XU4 Shifter Shield
power_distribution_board_bottom
power_distribution_board_top
USB_hub_support
battery_indicator
on-off_push-button
LVD_board
carter_rear
carter_cam

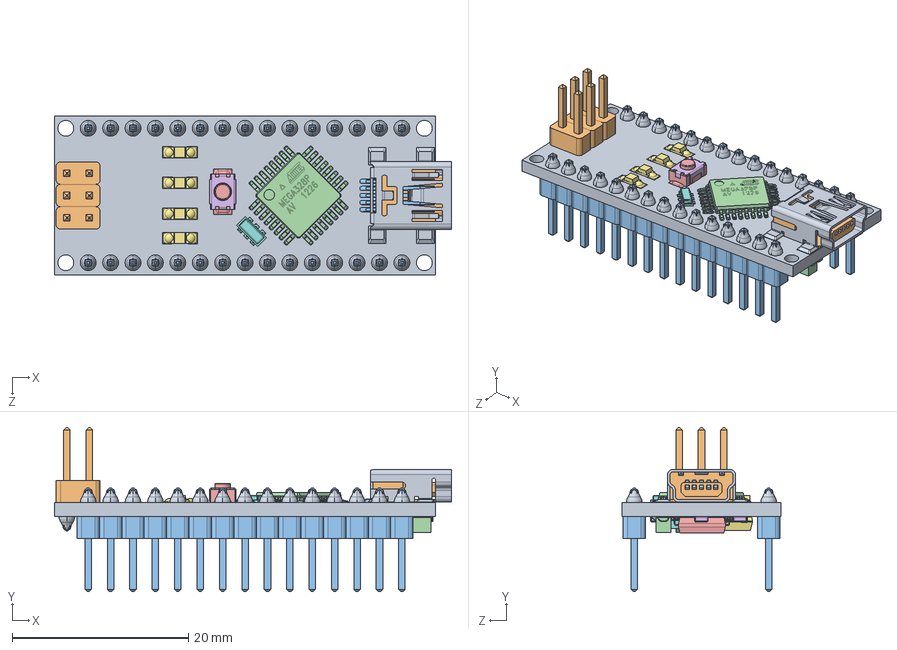
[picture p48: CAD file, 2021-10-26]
CAD/arduino_nano/User Library-arduino_nano.sldasm
45.0 x 18.6 x 18.0 mm
User Library-arduino_nano_nano-board
User Library-arduino_nano_2pin_header__02 x 3
User Library-arduino_nano_15pin_header__ x 2
User Library-arduino_nano_atmega328
User Library-arduino_nano_ftdi FT232rl
User Library-arduino_nano_smt_resistor222 x 5
User Library-arduino_nano_led x 4
User Library-arduino_nano_16mhz crystal - measured
User Library-arduino_nano_MINIUSBSHELL
User Library-arduino_nano_MINIUSBCORE
User Library-arduino_nano_MINI USB CONTACT x 5
User Library-arduino_nano_cap106C x 2
User Library-arduino_nano_reset core
User Library-arduino_nano_reset shell
User Library-arduino_nano_nano - reg
User Library-arduino_nano_NANO DIODE
User Library-arduino_nano_189 RESISTOR PACK
User Library-arduino_nano_102 RESISTOR PACK

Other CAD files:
CAD/arduino_nano/User Library-arduino_nano_nano - reg.sldprt
CAD/cam_assembly/led_ring_support.SLDPRT
CAD/carter_assembly/carter_surface.SLDPRT
CAD/connectors/2.54_pin_female_headers.SLDPRT
CAD/arduino_nano/User Library-arduino_nano_102 RESISTOR PACK.sldprt
CAD/arduino_nano/User Library-arduino_nano_15pin_header__.sldprt
CAD/arduino_nano/User Library-arduino_nano_16mhz crystal - measured.sldprt
CAD/arduino_nano/User Library-arduino_nano_189 RESISTOR PACK.sldprt
CAD/arduino_nano/User Library-arduino_nano_2pin_header__02.sldprt
CAD/arduino_nano/User Library-arduino_nano_MINI USB CONTACT.sldprt
CAD/arduino_nano/User Library-arduino_nano_MINIUSBCORE.sldprt
CAD/arduino_nano/User Library-arduino_nano_MINIUSBSHELL.sldprt
CAD/arduino_nano/User Library-arduino_nano_NANO DIODE.sldprt
CAD/arduino_nano/User Library-arduino_nano_atmega328.sldprt
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

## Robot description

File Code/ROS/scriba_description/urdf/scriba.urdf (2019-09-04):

<?xml version="1.0"?>
	<robot name="scriba">
		<link name="base_link">
			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
		</link>
		
		<link name="carter">
			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
		</link>
		
		<joint name="base_link_to_carter" type="fixed">
			<parent link="base_link"/>
			<child link="carter"/>
			<origin xyz="0 0 0"/>
		</joint>

		<link name="front_wheel_support">
			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
		</link>
		
		<joint name="base_link_to_front_wheel_support" type="revolute">
   		<parent link="base_link"/>
   		<child link="front_wheel_support"/>
   		<origin rpy="0 0 0" xyz="0.2156 0 0"/>
   		<limit effort="1000.0" lower="-1.57080" upper="1.57080" velocity="0.5"/>
   		<axis xyz="0 0 1"/>
  		</joint>
  		
		<link name="motor">
			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
		</link>
		
		<joint name="front_wheel_support_to_motor" type="fixed">
			<parent link="front_wheel_support"/>
			<child link="motor"/>
			<origin xyz="0 0.016 0"/>
		</joint>

		<link name="front_wheel">
			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
		</link>
		
		<joint name="front_wheel_support_to_front_wheel" type="continuous">
			<parent link="front_wheel_support"/>
			<child link="front_wheel"/>
			<origin xyz="0 0 0"/>
			<axis xyz="0 1 0"/>
		</joint>
		
		<link name="left_rear_wheel">
			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
		</link>

		<link name="right_rear_wheel">
			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
		</link>

		<joint name="base_link_to_left_rear_wheel" type="continuous">
			<parent link="base_link"/>
			<child link="left_rear_wheel"/>
			<origin xyz="0 0.04920 0"/>
			<axis xyz="0 1 0"/>
		</joint>

		<joint name="base_link_to_right_rear_wheel" type="continuous">
			<parent link="base_link"/>
			<child link="right_rear_wheel"/>
			<origin xyz="0 -0.04920 0"/>
			<axis xyz="0 1 0"/>
		</joint>

		<link name="front_camera_support">
			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
		</link>

		<joint name="base_link_to_front_camera_support" type="fixed">
			<parent link="base_link"/>
			<child link="front_camera_support"/>
			<origin xyz="0.25697 0 0.06050"/>
		</joint>
		
		<link name="front_camera">
			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
		</link>		

		<joint name="front_camera_support_to_front_camera" type="revolute">
   		<parent link="front_camera_support"/>
   		<child link="front_camera"/>
   		<origin rpy="0 0 0" xyz="0.018 0 0.010"/>
   		<limit effort="1000.0" lower="0.75" upper="1.57080" velocity="0.5"/>
   		<axis xyz="0 1 0"/>
  		</joint>

		<link name="front_camera_img_origin"/>

		<joint name="front_camera_to_front_camera_img_origin" type="fixed">
			<parent link="front_camera"/>
			<child link="front_camera_img_origin"/>
			<origin xyz="0.01410 0 0.005"/>
		</joint>
		
		<link name="rear_camera_support">
			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
		</link>

		<joint name="base_link_to_rear_camera_support" type="fixed">
			<parent link="base_link"/>
			<child link="rear_camera_support"/>
			<origin xyz="-0.04177 0 0.06050"/>
		</joint>
		
		<link name="rear_camera">
			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
		</link>		

		<joint name="rear_camera_support_to_rear_camera" type="revolute">
   		<parent link="rear_camera_support"/>
   		<child link="rear_camera"/>
   		<origin rpy="0 -2.3208 0" xyz="-0.018 0 0.010"/>
   		<limit effort="1000.0" lower="0.75" upper="1.57080" velocity="0.5"/>
   		<axis xyz="0 1 0"/>
  		</joint>

		<link name="rear_camera_img_origin"/>

		<joint name="rear_camera_to_rear_camera_img_origin" type="fixed">
			<parent link="rear_camera"/>
			<child link="rear_camera_img_origin"/>
			<origin xyz="0.01410 0 0.005"/>
		</joint>

		<link name="slider_base">
			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
		</link>

		<joint name="base_link_to_slider_base" type="revolute">
   		<parent link="base_link"/>
   		<child link="slider_base"/>
   		<origin rpy="0 0 0" xyz="0 0 0.01670"/>
   		<limit effort="1000.0" lower="-0.11" upper="0.11" velocity="0.5"/>
   		<axis xyz="0 0 1"/>
  		</joint>

		<link name="slider">
			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
		</link>

		<joint name="slider_base_to_slider" type="prismatic">
   		<parent link="slider_base"/>
   		<child link="slider"/>
   		<origin rpy="0 0 0" xyz="0.13311 0 0.017"/>
   		<limit effort="1000.0" lower="-0.040" upper="0.040" velocity="0.5"/>
   		<axis xyz="0 1 0"/>
  		</joint>

		<link name="slider_camera_support">
			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
		</link>
		
		<joint name="slider_to_slider_camera_support" type="prismatic">
   		<parent link="slider"/>
   		<child link="slider_camera_support"/>
   		<origin rpy="0 0 0" xyz="-0.061 0 -0.004"/>
   		<limit effort="1000.0" lower="0" upper="-0.020" velocity="0.5"/>
   		<axis xyz="0 0 1"/>
  		</joint>
  		
		<link name="slider_camera">
			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
		</link>  		

		<joint name="slider_camera_support_to_slider_camera" type="revolute">
			<parent link="slider_camera_support"/>
			<child link="slider_camera"/>
			<origin xyz="0.025 0 0.001"/>
			<limit effort="1000.0" lower="-1.57080" upper="1.57080" velocity="0.5"/>
   		<axis xyz="0 1 0"/>
		</joint>

		<link name="slider_camera_img_origin"/>

		<joint name="slider_camera_to_slider_camera_img_origin" type="fixed">
			<parent link="slider_camera"/>
			<child link="slider_camera_img_origin"/>
			<origin xyz="0.01410 0 0.005"/>
		</joint>
	</robot>

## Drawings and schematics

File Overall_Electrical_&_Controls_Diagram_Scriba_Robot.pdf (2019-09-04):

Scriba Robot - Overall Electrical & Controls Diagram | Legend

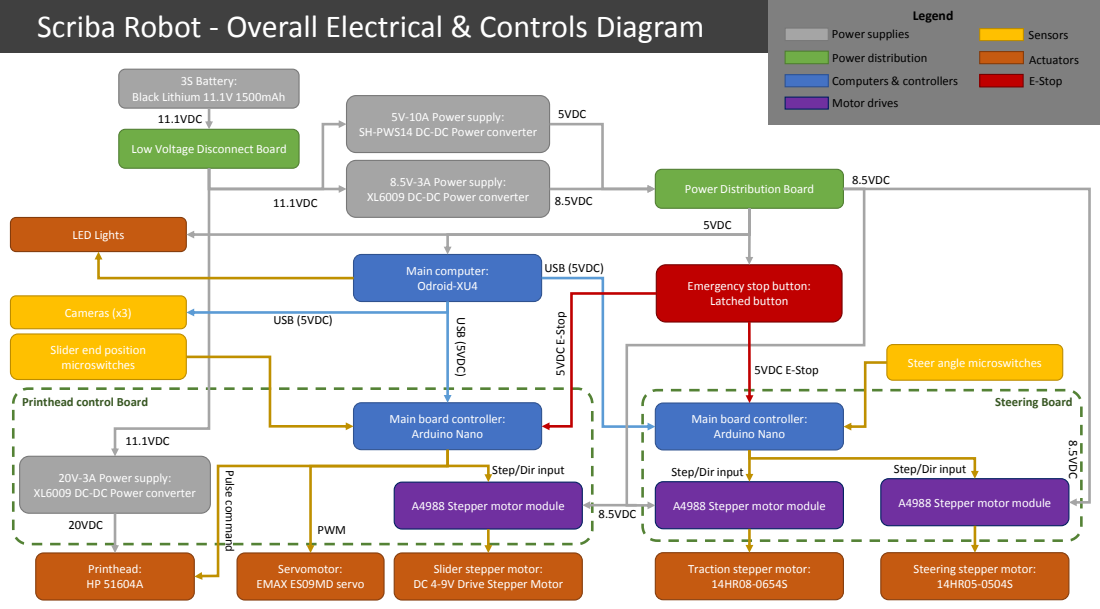
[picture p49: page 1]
3S Battery: Black Lithium 11.1V 1500mAh; Main computer: Odroid-XU4; A4988 Stepper motor module; Printhead: HP 51604A; Cameras (x3); LED Lights; 11.1VDC; 8.5VDC; 5VDC; USB (5VDC); 20VDC; 5VDC E-Stop; Step/Dir input; Printhead control Board; Steering Board; Power supplies; Power distribution; Computers & controllers; Motor drives; Sensors; Actuators; E-Stop; Servomotor: EMAX ES09MD servo; PWM; Pulse command

5V-10A Power supply:
SH-PWS14 DC-DC Power converter

Low Voltage Disconnect Board

8.5V-3A Power supply:
XL6009 DC-DC Power converter

Power Distribution Board

Emergency stop button:
Latched button

Slider end position
microswitches

Steer angle microswitches

Main board controller:
Arduino Nano

20V-3A Power supply:

A4988 Stepper motor module

Slider stepper motor:
DC 4-9V Drive Stepper Motor

Traction stepper motor:

Steering stepper motor:

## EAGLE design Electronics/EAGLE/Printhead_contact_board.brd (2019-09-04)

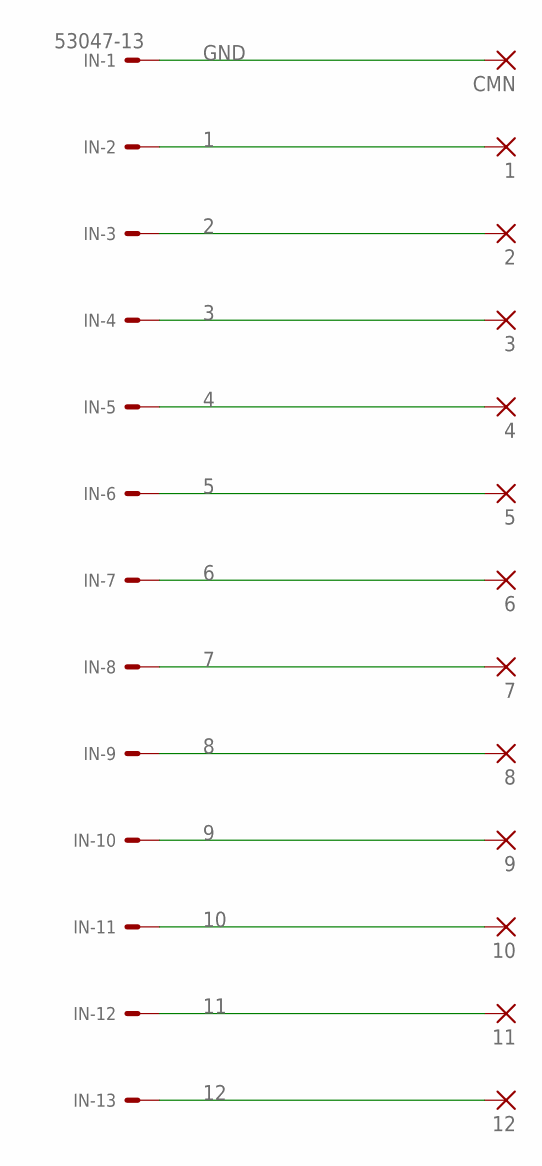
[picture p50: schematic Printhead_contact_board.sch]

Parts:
1, 2, 3, 4, 5, 6, 7, 8, 9, 10, 11, 12: SMD2; SMD1,27-2,54
CMN: SMD2; SMD1,27-2,54
IN: 53047-13

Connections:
1: 1.1, IN.2
2: 2.1, IN.3
3: 3.1, IN.4
4: 4.1, IN.5
5: 5.1, IN.6
6: 6.1, IN.7
7: 7.1, IN.8
8: 8.1, IN.9
9: 9.1, IN.10
10: 10.1, IN.11
11: 11.1, IN.12
12: 12.1, IN.13
GND: CMN.1, IN.1

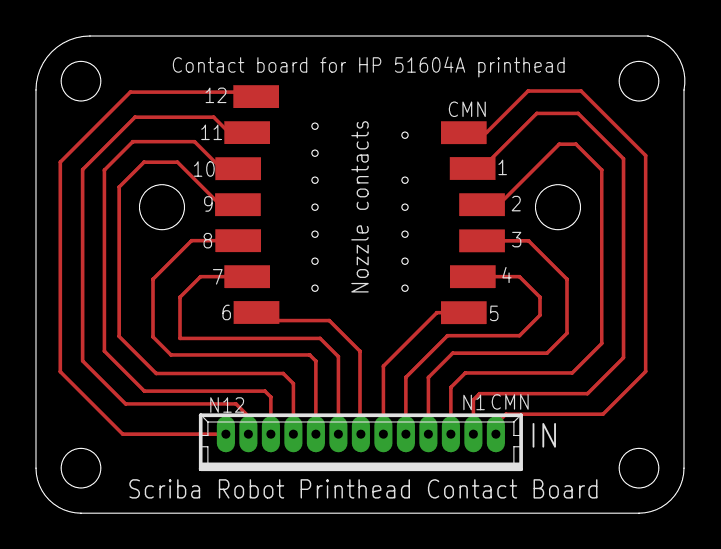
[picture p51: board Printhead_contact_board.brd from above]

Board: 2 copper layers, 36.0 x 26.5 mm, 14 parts (0 on the bottom side), 13 nets.

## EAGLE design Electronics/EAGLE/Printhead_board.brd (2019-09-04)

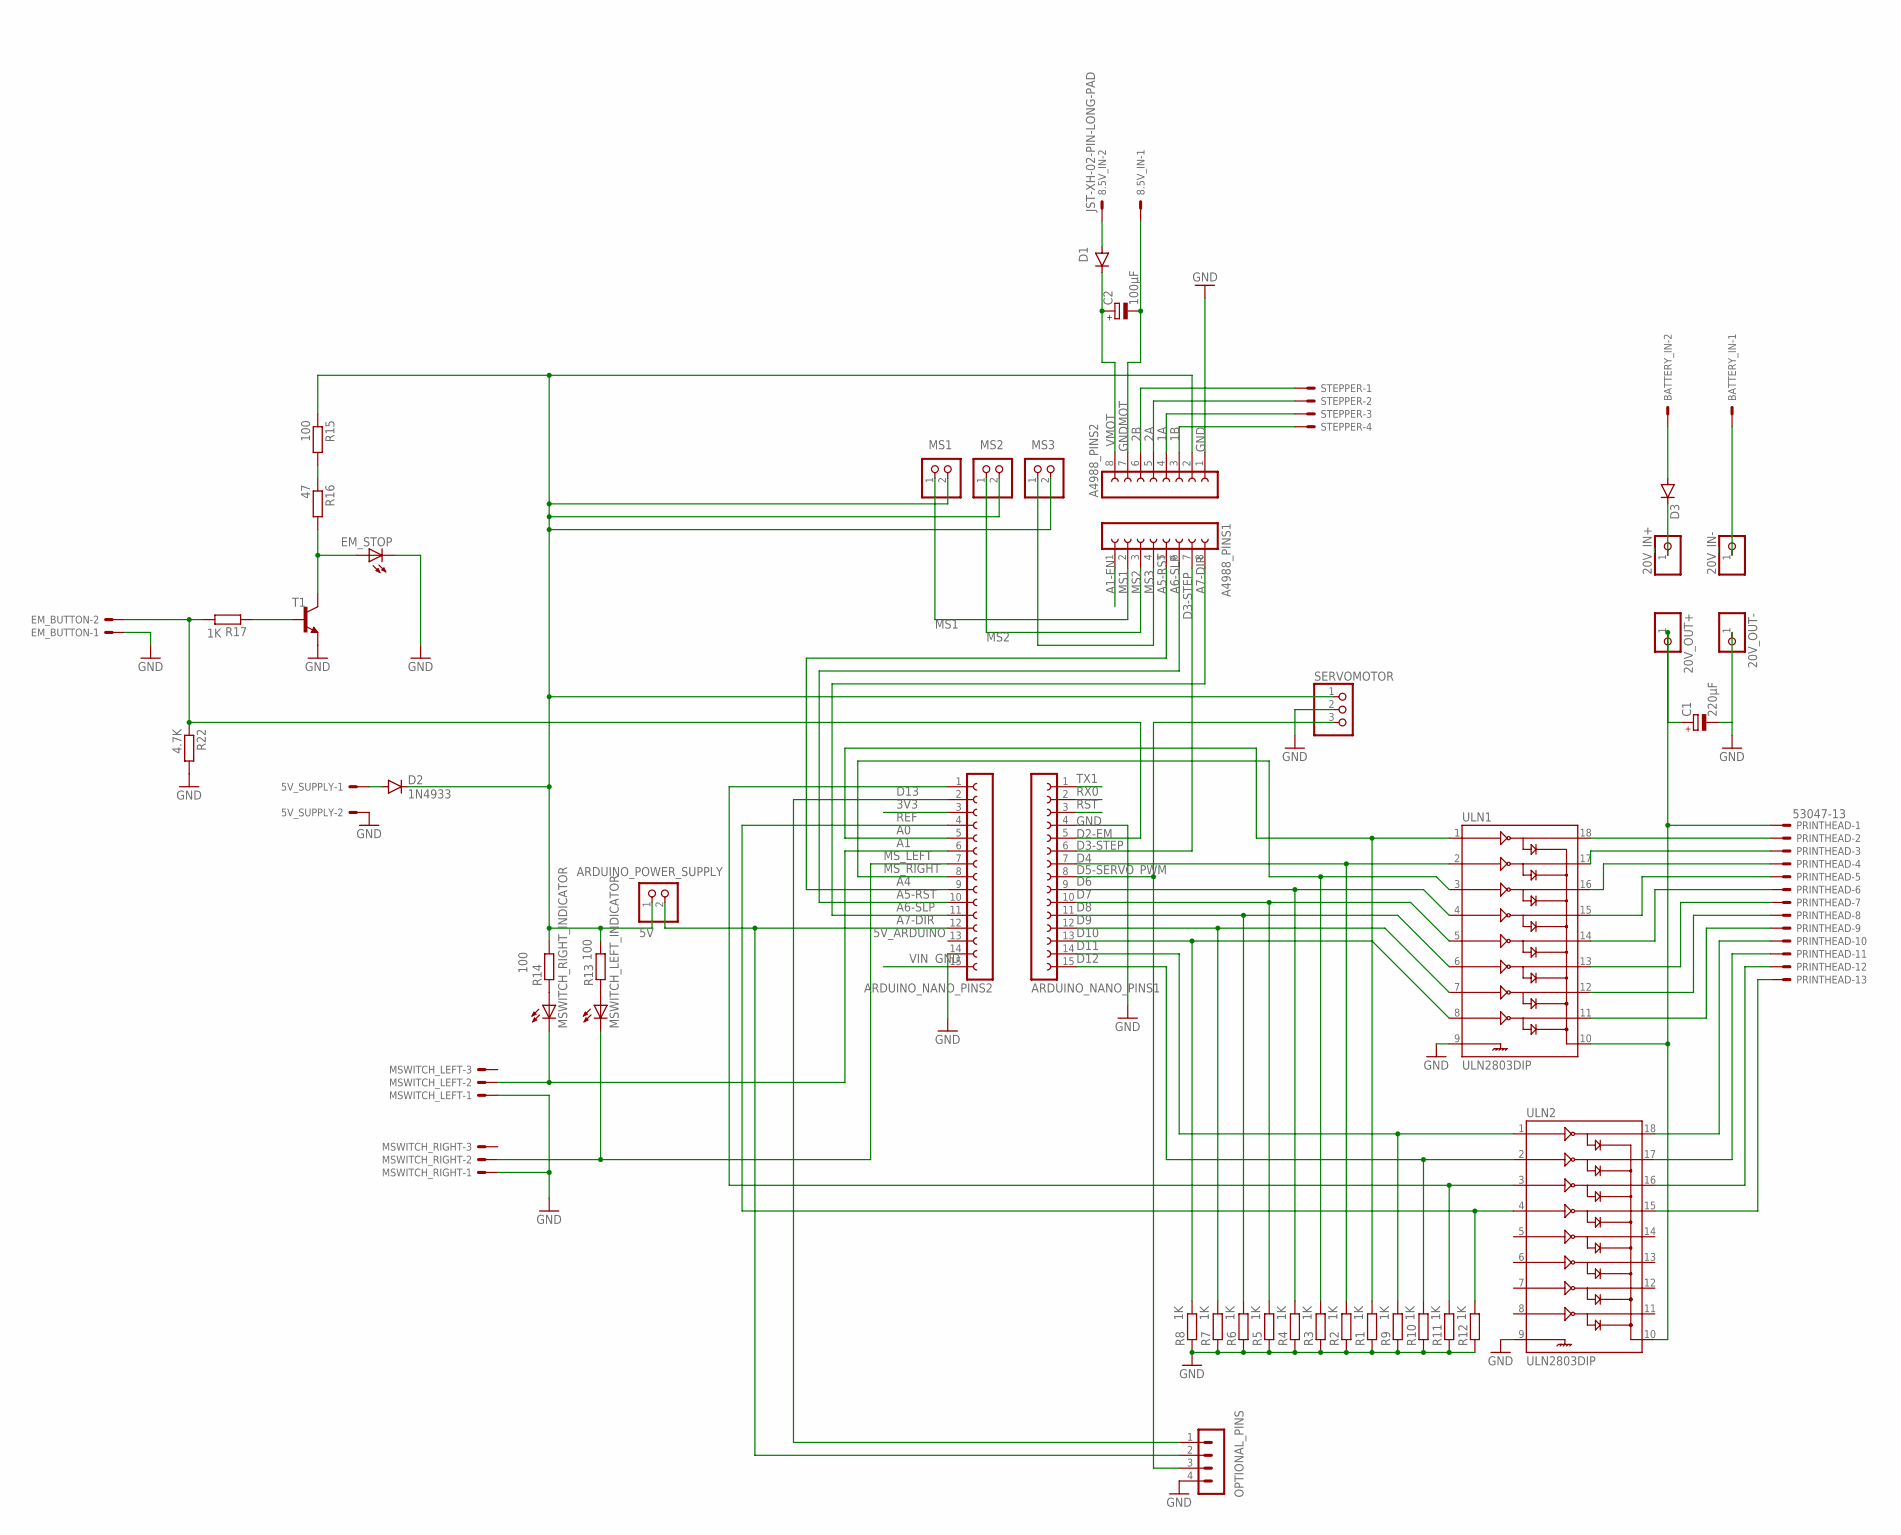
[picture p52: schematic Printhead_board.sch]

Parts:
5V_SUPPLY, 8.5V_IN: JST-XH-02-PIN-LONG-PAD; JST-XH-02-PACKAGE-LONG-PAD
20V_IN+, 20V_IN-, 20V_OUT+, 20V_OUT-: PINHD-1X1; 1X01
A4988_PINS1, A4988_PINS2: FE08-1; FE08
ARDUINO_NANO_PINS1, ARDUINO_NANO_PINS2: FE15-1; FE15
ARDUINO_POWER_SUPPLY: PINHD-1X2; 1X02
BATTERY_IN: JST-XH-02-PIN-ROUND-PAD; JST-XH-02-PACKAGE-ROUND-PAD
C1: 220µF; E5-10,5
C2: 100µF; SANYO-OSCON_E
D1: DIODE-DO15-12; DO15-12
D2: 1N4933; DO41-10
D3: DIODE-DO201-15; DO201-15
EM_BUTTON: JST-XH-02-PIN-LONG-PAD; JST-XH-02-PACKAGE-LONG-PAD
EM_STOP: LED5MM
MS1, MS2, MS3: PINHD-1X2; 1X02
MSWITCH_LEFT: JST-XH-03-PIN-LONG-PAD; JST-XH-03-PACKAGE-LONG-PAD
MSWITCH_LEFT_INDICATOR: LED5MM
MSWITCH_RIGHT: JST-XH-03-PIN-LONG-PAD; JST-XH-03-PACKAGE-LONG-PAD
MSWITCH_RIGHT_INDICATOR: LED5MM
OPTIONAL_PINS: MA04-1
PRINTHEAD: 53047-13
R1, R2, R3, R4, R5, R6, R7, R8, R9, R10, R11, R12, R17: 1K; 0207/7
R13, R14, R15: 100; 0207/7
R16: 47; 0207/7
R22: 4.7K; 0207/7
SERVOMOTOR: PINHD-1X3; 1X03
STEPPER: JST-XH-04-PIN-LONG-PAD; JST-XH-04-PACKAGE-LONG-PAD
T1: 2N2222; TO92-EBC-OVAL
ULN1, ULN2: ULN2803DIP; DIL18

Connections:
1A: A4988_PINS2.4, STEPPER.3
1B: A4988_PINS2.3, STEPPER.4
2A: A4988_PINS2.5, STEPPER.2
2B: A4988_PINS2.6, STEPPER.1
3V3: ARDUINO_NANO_PINS2.2, OPTIONAL_PINS.1
5V: A4988_PINS2.2, ARDUINO_POWER_SUPPLY.1, D2.C, MS1.2, MS2.2, MS3.2, R13.2, R14.2, R15.1, SERVOMOTOR.1
5V_ARDUINO: ARDUINO_NANO_PINS2.12, ARDUINO_POWER_SUPPLY.2, OPTIONAL_PINS.2
A0: ARDUINO_NANO_PINS2.4, R12.2, ULN2.4
A1: ARDUINO_NANO_PINS2.5, R1.2, ULN1.1
A1-EN: A4988_PINS1.1
A4: ARDUINO_NANO_PINS2.8, R3.2, ULN1.3
A5-RST: A4988_PINS1.5, ARDUINO_NANO_PINS2.9
A6-SLP: A4988_PINS1.6, ARDUINO_NANO_PINS2.10
A7-DIR: A4988_PINS1.8, ARDUINO_NANO_PINS2.11
D2-EM: ARDUINO_NANO_PINS1.5, EM_BUTTON.2, R17.2, R22.1
D3-STEP: A4988_PINS1.7, ARDUINO_NANO_PINS1.6
D4: ARDUINO_NANO_PINS1.7, R2.2, ULN1.2
D5-SERVO_PWM: ARDUINO_NANO_PINS1.8, OPTIONAL_PINS.3, SERVOMOTOR.3
D6: ARDUINO_NANO_PINS1.9, R4.2, ULN1.4
D7: ARDUINO_NANO_PINS1.10, R5.2, ULN1.5
D8: ARDUINO_NANO_PINS1.11, R6.2, ULN1.6
D9: ARDUINO_NANO_PINS1.12, R7.2, ULN1.7
D10: ARDUINO_NANO_PINS1.13, R8.2, ULN1.8
D11: ARDUINO_NANO_PINS1.14, R9.2, ULN2.1
D12: ARDUINO_NANO_PINS1.15, R10.2, ULN2.2
D13: ARDUINO_NANO_PINS2.1, R11.2, ULN2.3
GND: 5V_SUPPLY.2, 20V_OUT-.1, A4988_PINS2.1, ARDUINO_NANO_PINS1.4, ARDUINO_NANO_PINS2.14, C1.-, EM_BUTTON.1, EM_STOP.K (C), MSWITCH_LEFT.1, MSWITCH_RIGHT.1, OPTIONAL_PINS.4, R1.1, R2.1, R3.1, R4.1, R5.1, R6.1, R7.1, R8.1, R9.1, R10.1, R11.1, R12.1, R22.2, SERVOMOTOR.2, T1.E, ULN1.9, ULN2.9
GNDMOT: 8.5V_IN.1, A4988_PINS2.7, C2.-
MS1: A4988_PINS1.2, MS1.1
MS2: A4988_PINS1.3, MS2.1
MS3: A4988_PINS1.4, MS3.1
MS_LEFT: ARDUINO_NANO_PINS2.6, MSWITCH_LEFT.2, MSWITCH_RIGHT_INDICATOR.K (C)
MS_RIGHT: ARDUINO_NANO_PINS2.7, MSWITCH_LEFT_INDICATOR.K (C), MSWITCH_RIGHT.2
N1: PRINTHEAD.2, ULN1.18
N12: PRINTHEAD.13, ULN2.15
unnamed: EM_STOP.A, R16.2, T1.C
unnamed: R17.1, T1.B
unnamed: R15.2, R16.1
unnamed: BATTERY_IN.2, D3.A
unnamed: 5V_SUPPLY.1, D2.A
unnamed: PRINTHEAD.3, ULN1.17
unnamed: PRINTHEAD.4, ULN1.16
unnamed: PRINTHEAD.5, ULN1.15
unnamed: PRINTHEAD.6, ULN1.14
unnamed: PRINTHEAD.7, ULN1.13
unnamed: PRINTHEAD.8, ULN1.12
unnamed: PRINTHEAD.9, ULN1.11
unnamed: PRINTHEAD.10, ULN2.18
unnamed: PRINTHEAD.11, ULN2.17
unnamed: PRINTHEAD.12, ULN2.16
unnamed: 8.5V_IN.2, D1.A
unnamed: MSWITCH_LEFT_INDICATOR.A, R13.1
unnamed: MSWITCH_RIGHT_INDICATOR.A, R14.1
unnamed: 20V_IN-.1, BATTERY_IN.1
unnamed: 20V_OUT+.1, C1.+, PRINTHEAD.1, ULN1.10, ULN2.10
unnamed: 20V_IN+.1, D3.C
REF: ARDUINO_NANO_PINS2.3
RST: ARDUINO_NANO_PINS1.3
RX0: ARDUINO_NANO_PINS1.2
TX1: ARDUINO_NANO_PINS1.1
VIN: ARDUINO_NANO_PINS2.15
VMOT: A4988_PINS2.8, C2.+, D1.C

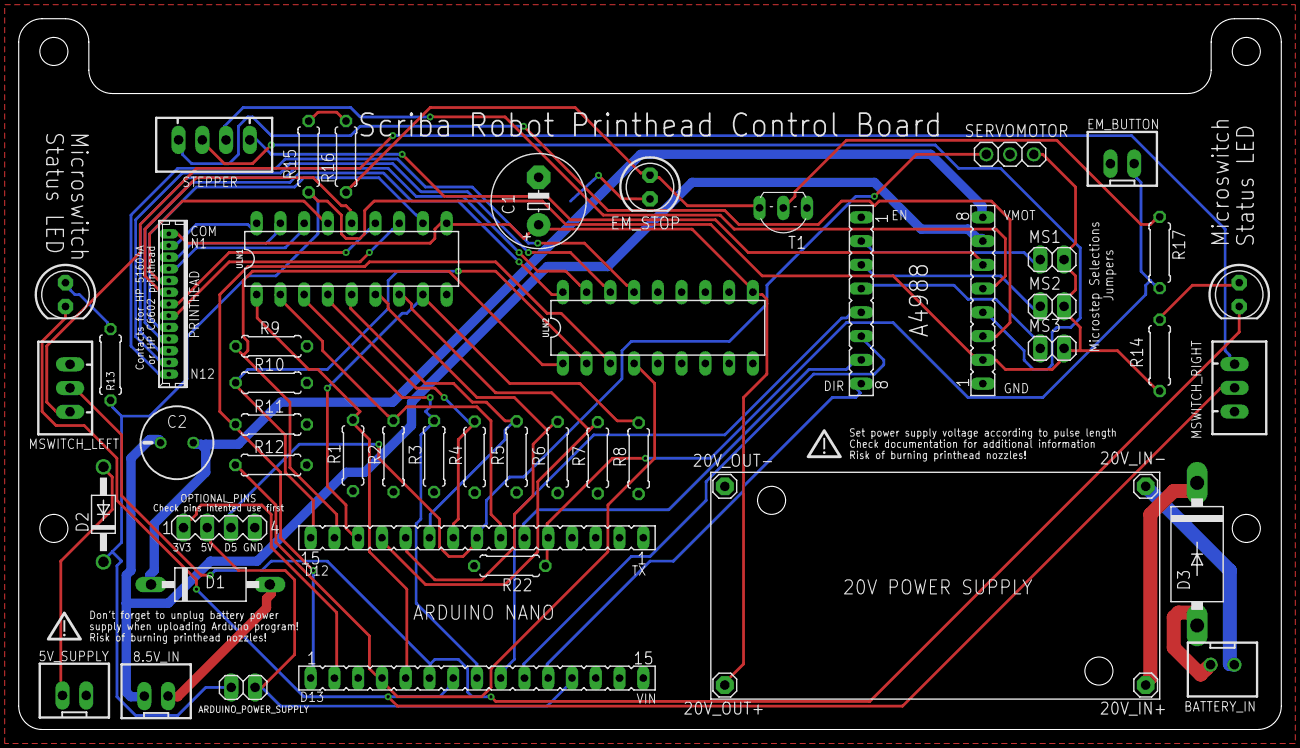
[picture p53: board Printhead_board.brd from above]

Board: 2 copper layers, 135.0 x 76.0 mm, 51 parts (0 on the bottom side), 56 nets.

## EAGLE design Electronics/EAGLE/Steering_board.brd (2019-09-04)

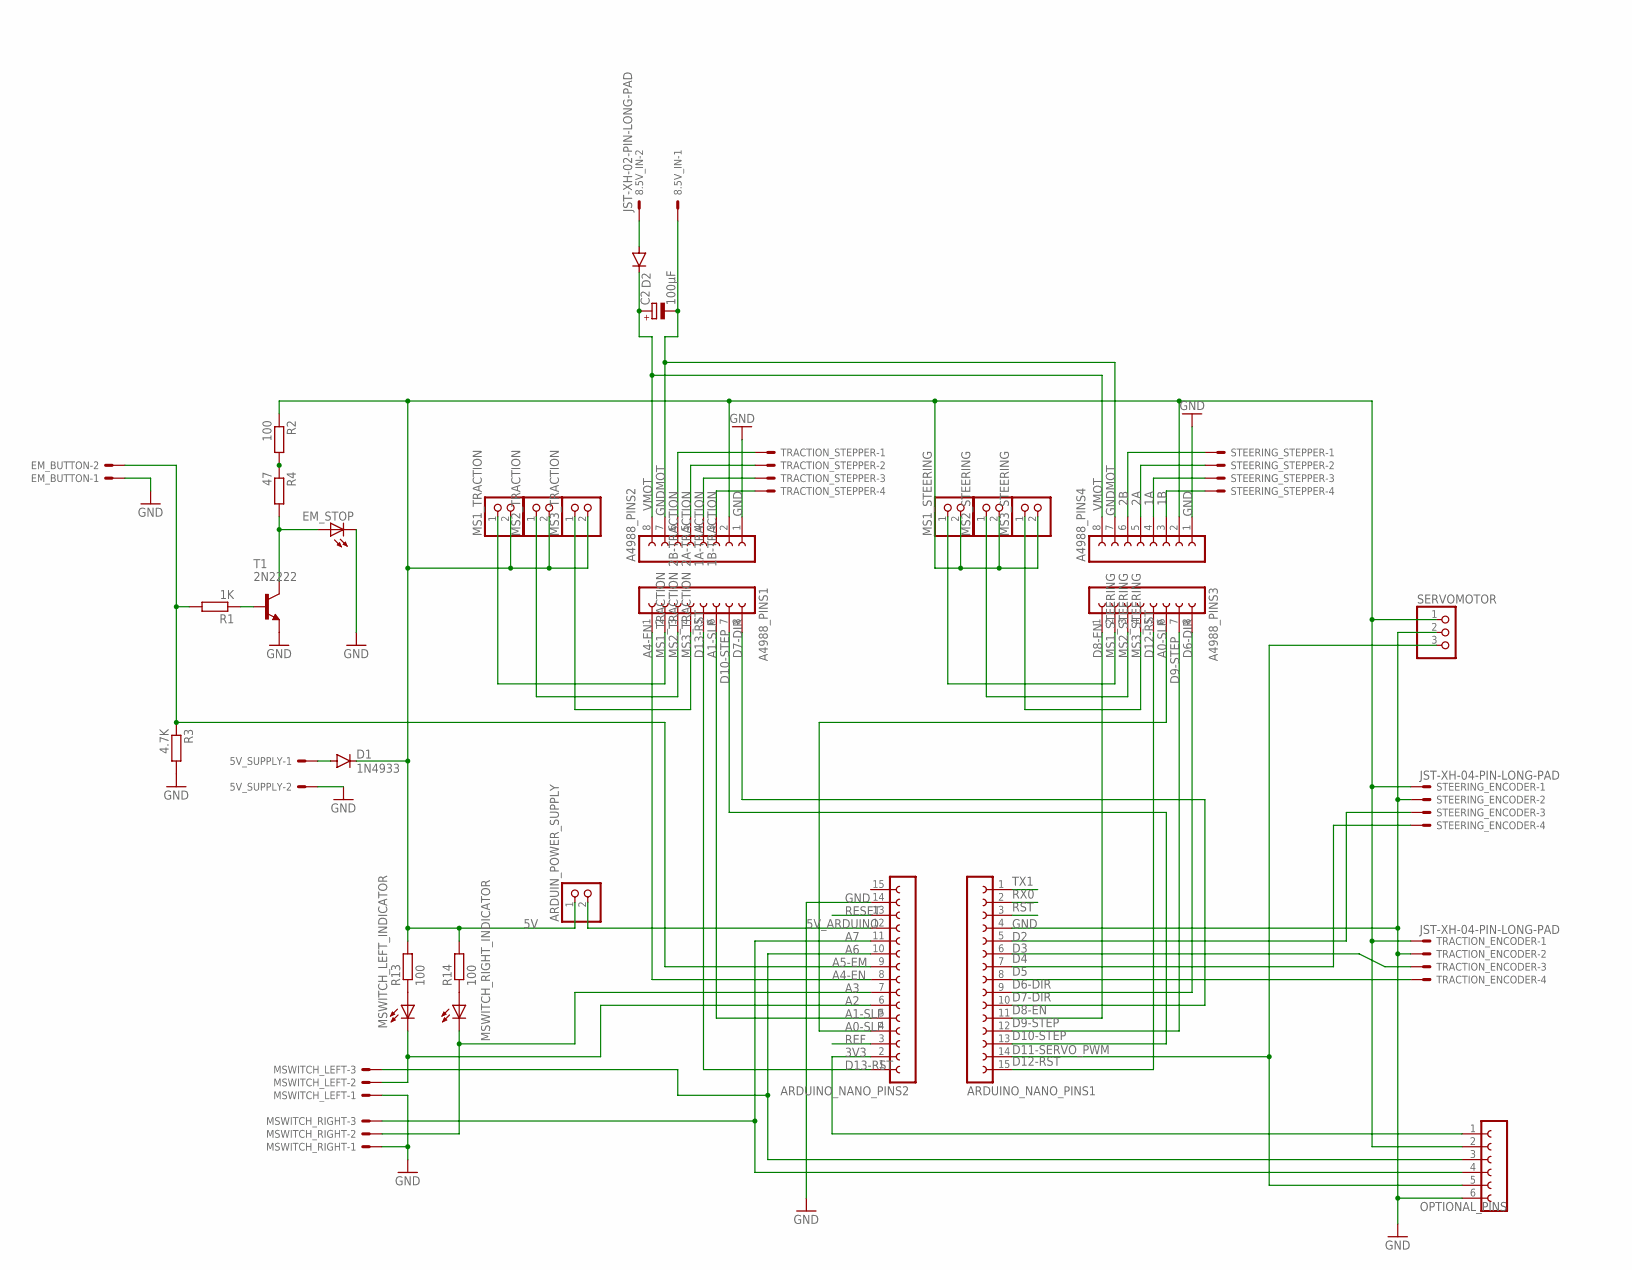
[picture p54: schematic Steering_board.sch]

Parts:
5V_SUPPLY, 8.5V_IN: JST-XH-02-PIN-LONG-PAD; JST-XH-02-PACKAGE-LONG-PAD
A4988_PINS1, A4988_PINS2, A4988_PINS3, A4988_PINS4: FE08-1; FE08
ARDUINO_NANO_PINS1, ARDUINO_NANO_PINS2: FE15-1; FE15
ARDUIN_POWER_SUPPLY: PINHD-1X2; 1X02
C2: 100µF; SANYO-OSCON_E
D1: 1N4933; DO41-10
D2: DIODE-DO15-12; DO15-12
EM_BUTTON: JST-XH-02-PIN-LONG-PAD; JST-XH-02-PACKAGE-LONG-PAD
EM_STOP: LED5MM
MS1_STEERING, MS1_TRACTION, MS2_STEERING, MS2_TRACTION, MS3_STEERING, MS3_TRACTION: PINHD-1X2; 1X02
MSWITCH_LEFT: JST-XH-03-PIN-LONG-PAD; JST-XH-03-PACKAGE-LONG-PAD
MSWITCH_LEFT_INDICATOR: LED5MM
MSWITCH_RIGHT: JST-XH-03-PIN-LONG-PAD; JST-XH-03-PACKAGE-LONG-PAD
MSWITCH_RIGHT_INDICATOR: LED5MM
OPTIONAL_PINS: FE06-1; FE06
R1: 1K; 0207/7
R2, R13, R14: 100; 0207/7
R3: 4.7K; 0207/7
R4: 47; 0207/7
SERVOMOTOR: PINHD-1X3; 1X03
STEERING_ENCODER: JST-XH-04-PIN-LONG-PAD; JST-XH-04-PACKAGE-LONG-PAD
STEERING_STEPPER: JST-XH-04-PIN-LONG-PAD; JST-XH-04-PACKAGE-LONG-PAD
T1: 2N2222; TO92-EBC-OVAL
TRACTION_ENCODER: JST-XH-04-PIN-LONG-PAD; JST-XH-04-PACKAGE-LONG-PAD
TRACTION_STEPPER: JST-XH-04-PIN-LONG-PAD; JST-XH-04-PACKAGE-LONG-PAD

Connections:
1A: A4988_PINS4.4, STEERING_STEPPER.3
1A-TRACTION: A4988_PINS2.4, TRACTION_STEPPER.3
1B: A4988_PINS4.3, STEERING_STEPPER.4
1B-TRACTION: A4988_PINS2.3, TRACTION_STEPPER.4
2A: A4988_PINS4.5, STEERING_STEPPER.2
2A-TRACTION: A4988_PINS2.5, TRACTION_STEPPER.2
2B: A4988_PINS4.6, STEERING_STEPPER.1
2B-TRACTION: A4988_PINS2.6, TRACTION_STEPPER.1
3V3: ARDUINO_NANO_PINS2.2, OPTIONAL_PINS.1
5V: A4988_PINS2.2, A4988_PINS4.2, ARDUIN_POWER_SUPPLY.1, D1.C, MS1_STEERING.2, MS1_TRACTION.2, MS2_STEERING.2, MS2_TRACTION.2, MS3_STEERING.2, MS3_TRACTION.2, OPTIONAL_PINS.2, R2.1, R13.2, R14.2, SERVOMOTOR.1, STEERING_ENCODER.1, TRACTION_ENCODER.1
5V_ARDUINO: ARDUINO_NANO_PINS2.12, ARDUIN_POWER_SUPPLY.2
A0-SLP: A4988_PINS3.6, ARDUINO_NANO_PINS2.4
A1-SLP: A4988_PINS1.6, ARDUINO_NANO_PINS2.5
A2: ARDUINO_NANO_PINS2.6, MSWITCH_LEFT.2, MSWITCH_LEFT_INDICATOR.K (C)
A3: ARDUINO_NANO_PINS2.7, MSWITCH_RIGHT.2, MSWITCH_RIGHT_INDICATOR.K (C)
A4-EN: A4988_PINS1.1, ARDUINO_NANO_PINS2.8
A5-EM: ARDUINO_NANO_PINS2.9, EM_BUTTON.2, R1.2, R3.1
A6: ARDUINO_NANO_PINS2.10, MSWITCH_LEFT.3, OPTIONAL_PINS.3
A7: ARDUINO_NANO_PINS2.11, MSWITCH_RIGHT.3, OPTIONAL_PINS.4
D2: ARDUINO_NANO_PINS1.5, STEERING_ENCODER.3
D3: ARDUINO_NANO_PINS1.6, TRACTION_ENCODER.3
D4: ARDUINO_NANO_PINS1.7, STEERING_ENCODER.4
D5: ARDUINO_NANO_PINS1.8, TRACTION_ENCODER.4
D6-DIR: A4988_PINS3.8, ARDUINO_NANO_PINS1.9
D7-DIR: A4988_PINS1.8, ARDUINO_NANO_PINS1.10
D8-EN: A4988_PINS3.1, ARDUINO_NANO_PINS1.11
D9-STEP: A4988_PINS3.7, ARDUINO_NANO_PINS1.12
D10-STEP: A4988_PINS1.7, ARDUINO_NANO_PINS1.13
D11-SERVO_PWM: ARDUINO_NANO_PINS1.14, OPTIONAL_PINS.5, SERVOMOTOR.3
D12-RST: A4988_PINS3.5, ARDUINO_NANO_PINS1.15
D13-RST: A4988_PINS1.5, ARDUINO_NANO_PINS2.1
GND: 5V_SUPPLY.2, A4988_PINS2.1, A4988_PINS4.1, ARDUINO_NANO_PINS1.4, ARDUINO_NANO_PINS2.14, EM_BUTTON.1, EM_STOP.K (C), MSWITCH_LEFT.1, MSWITCH_RIGHT.1, OPTIONAL_PINS.6, R3.2, SERVOMOTOR.2, STEERING_ENCODER.2, T1.E, TRACTION_ENCODER.2
GNDMOT: 8.5V_IN.1, A4988_PINS2.7, A4988_PINS4.7, C2.-
MS1_STEERING: A4988_PINS3.2, MS1_STEERING.1
MS1_TRACTION: A4988_PINS1.2, MS1_TRACTION.1
MS2_STEERING: A4988_PINS3.3, MS2_STEERING.1
MS2_TRACTION: A4988_PINS1.3, MS2_TRACTION.1
MS3_STEERING: A4988_PINS3.4, MS3_STEERING.1
MS3_TRACTION: A4988_PINS1.4, MS3_TRACTION.1
unnamed: 8.5V_IN.2, D2.A
unnamed: 5V_SUPPLY.1, D1.A
unnamed: R2.2, R4.1
unnamed: EM_STOP.A, R4.2, T1.C
unnamed: R1.1, T1.B
unnamed: MSWITCH_LEFT_INDICATOR.A, R13.1
unnamed: MSWITCH_RIGHT_INDICATOR.A, R14.1
REF: ARDUINO_NANO_PINS2.3
RESET: ARDUINO_NANO_PINS2.13
RST: ARDUINO_NANO_PINS1.3
RX0: ARDUINO_NANO_PINS1.2
TX1: ARDUINO_NANO_PINS1.1
VMOT: A4988_PINS2.8, A4988_PINS4.8, C2.+, D2.C

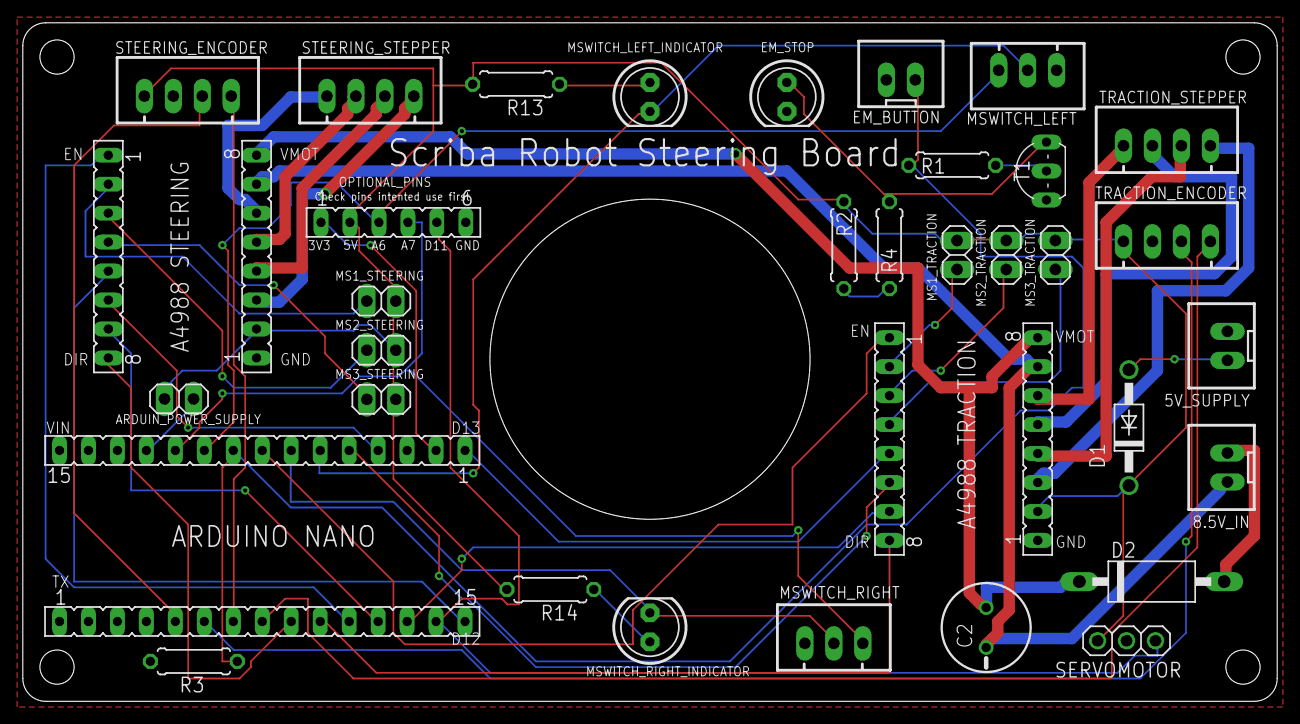
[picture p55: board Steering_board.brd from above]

Board: 2 copper layers, 110.0 x 59.5 mm, 37 parts (0 on the bottom side), 47 nets.

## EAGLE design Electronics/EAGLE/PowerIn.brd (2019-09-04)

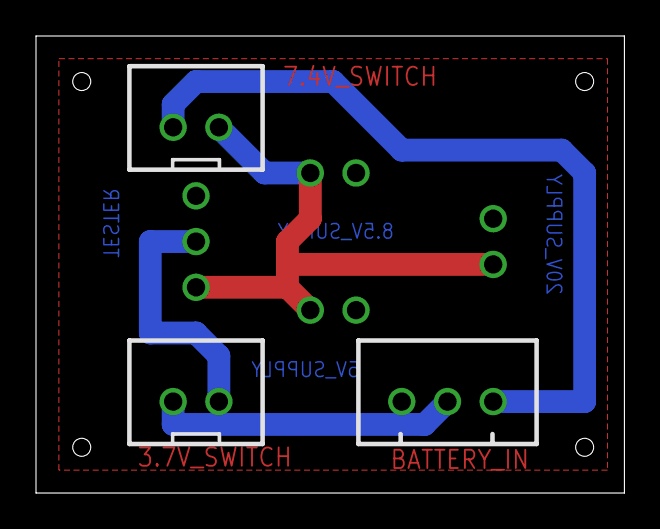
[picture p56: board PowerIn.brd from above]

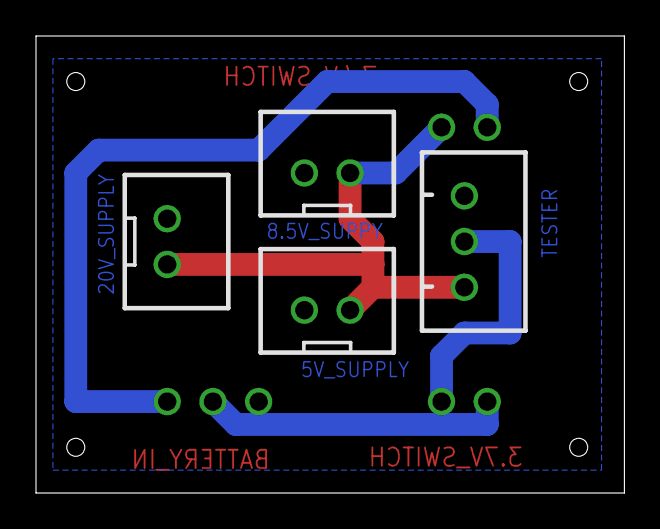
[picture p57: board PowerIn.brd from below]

Board: 2 copper layers, 32.7 x 25.4 mm, 7 parts (4 on the bottom side), 5 nets.

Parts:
3.7V_SWITCH, 5V_SUPPLY, 7.4V_SWITCH, 8.5V_SUPPY, 20V_SUPPLY: JST-XH-02-PIN-ROUND-PAD; JST-XH-02-PACKAGE-ROUND-PAD
BATTERY_IN: JST-XH-03-PIN-ROUND-PAD; JST-XH-03-PACKAGE-ROUND-PAD
TESTER: JST-XH-03-PIN-ROUND-PAD; JST-XH-03-PACKAGE-ROUND-PAD

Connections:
GND: 5V_SUPPLY.1, 8.5V_SUPPY.1, 20V_SUPPLY.1, BATTERY_IN.1, TESTER.1
unnamed: 7.4V_SWITCH.1, BATTERY_IN.3
unnamed: 3.7V_SWITCH.1, BATTERY_IN.2
unnamed: 3.7V_SWITCH.2, TESTER.2
unnamed: 5V_SUPPLY.2, 7.4V_SWITCH.2, 8.5V_SUPPY.2, 20V_SUPPLY.2, TESTER.3

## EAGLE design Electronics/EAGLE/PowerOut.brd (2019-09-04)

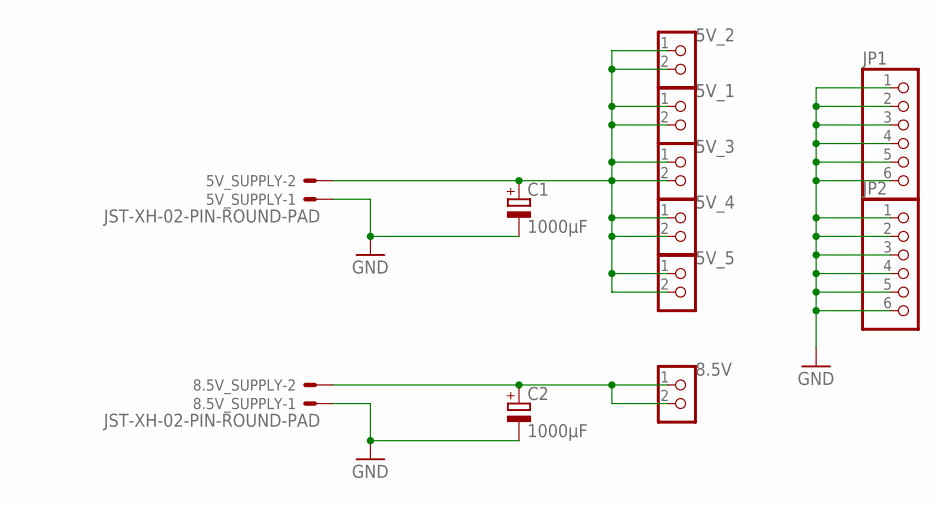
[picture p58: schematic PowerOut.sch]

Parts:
5V_1, 5V_2, 5V_3, 5V_4, 5V_5, 8.5V: CON_TERMINAL_BLOCK_02-5MM; TERMINAL_BLOCK_2P_5
5V_SUPPLY, 8.5V_SUPPLY: JST-XH-02-PIN-ROUND-PAD; JST-XH-02-PACKAGE-ROUND-PAD
C1, C2: 1000µF; E5-10,5
JP1, JP2: PINHD-1X6; 1X06

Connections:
GND: 5V_SUPPLY.1, 8.5V_SUPPLY.1, C1.-, C2.-, JP1.1, JP1.2, JP1.3, JP1.4, JP1.5, JP1.6, JP2.1, JP2.2, JP2.3, JP2.4, JP2.5, JP2.6
unnamed: 5V_1.1, 5V_1.2, 5V_2.1, 5V_2.2, 5V_3.1, 5V_3.2, 5V_4.1, 5V_4.2, 5V_5.1, 5V_5.2, 5V_SUPPLY.2, C1.+
unnamed: 8.5V.1, 8.5V.2, 8.5V_SUPPLY.2, C2.+

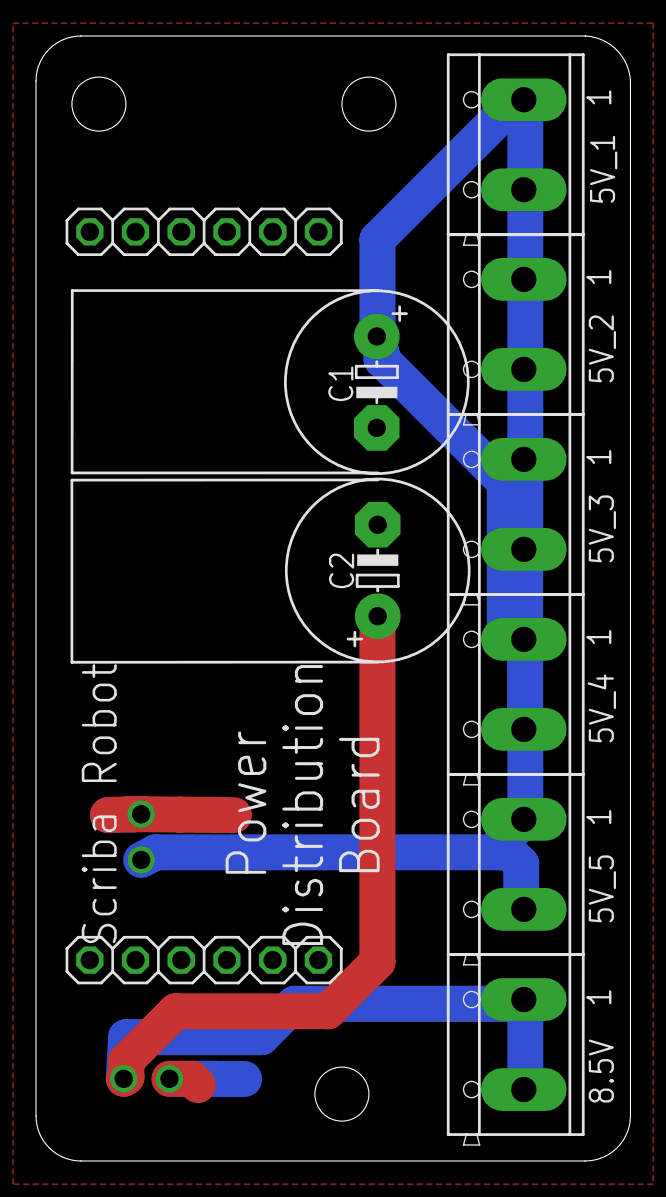
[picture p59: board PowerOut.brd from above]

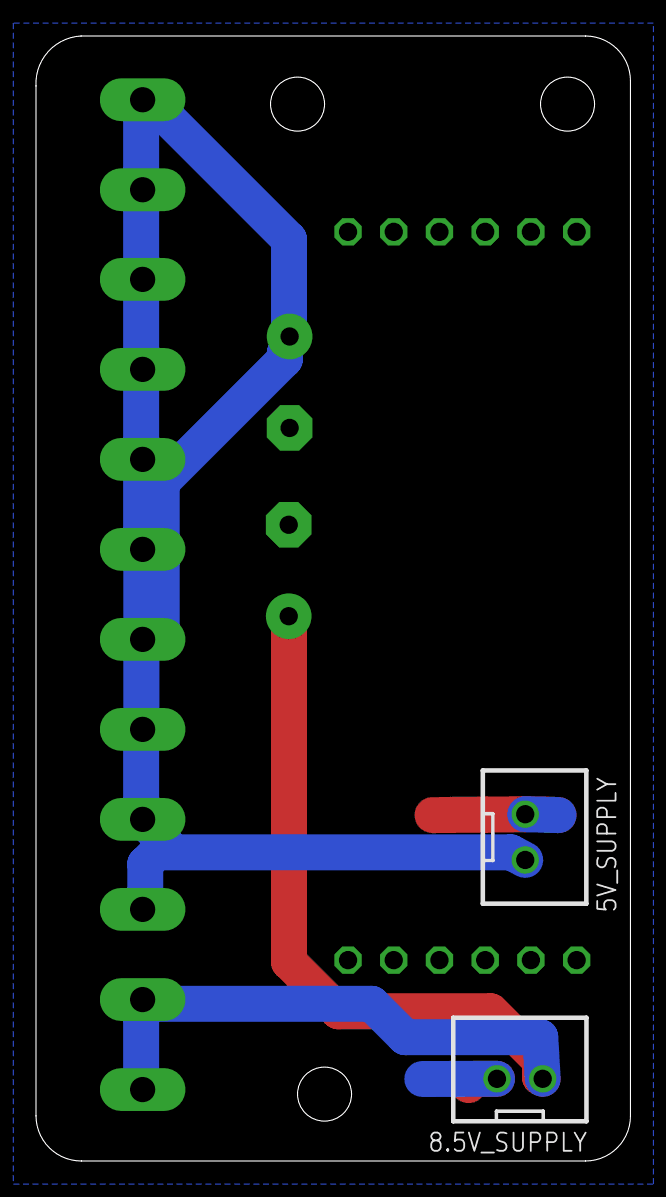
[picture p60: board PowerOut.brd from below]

Board: 2 copper layers, 33.0 x 62.5 mm, 12 parts (2 on the bottom side), 3 nets.

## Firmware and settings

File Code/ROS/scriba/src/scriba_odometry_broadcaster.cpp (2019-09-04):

#include "ros/ros.h"
#include "nav_msgs/Odometry.h"  
#include "scriba_msgs/data_odom.h"
#include "tf/transform_broadcaster.h"
#include "sensor_msgs/JointState.h"
#include <cmath>

double length = 0.2156;						//Length between front wheel and rear wheels, in meters					
double wheel_radius = 0.025;				//Front wheel radius in meters
float microstepSteeringRatio = 0.5;  	//Microstepping configuration for steering motor
float microstepTractionRatio = 1;  	//Microstepping configuration for traction motor
const float pi = 3.14159;     			//It's just Pi, what did you expect?
const float two_pi = 6.28318;				//And it's 2 times Pi...

double frontWheelDistance = 0;			//Front wheel traveled distance in meters
double tractionSteps = 0;					//Front wheel traveled steps
double phi = 0;								//Front wheel steer angle in rad

double rate = 10.0;
bool publish_tf = true;
double x_pos = 0.0;
double y_pos = 0.0;
double dt = 0.0;
double dx = 0.0;
double dy = 0.0;
double alpha = 0.0;
double omega = 0.0;
double vx = 0.0;
double vy = 0.0;
double vth = 0.0;
char base_link[] = "/base_link";
char odom[] = "/odom";


class SubscribeAndPublish
{
public:
  SubscribeAndPublish()
  {
	//Topic you want to publish
	odom_pub = n.advertise<nav_msgs::Odometry>("odom", 50);
	odom_joint_pub = n.advertise<sensor_msgs::JointState>("joint_states", 1); //Create joint publisher	
	
	//Topic you want to subscribe
	odom_data_sub = n.subscribe("odom_data", 1000, &SubscribeAndPublish::callback, this);
	
	current_time = ros::Time::now();
  }

  void callback(const scriba_msgs::data_odom& odom_data_msg)
  {
  	//Get data from message and compute displacement
  	current_time = odom_data_msg.header.stamp;													//Get odometry data time stamp
	dt = odom_data_msg.durationMillis/1000;														//Get odometry data sample durations and converts from milliseconds to seconds
	tractionSteps = odom_data_msg.tractionSteps;													//Get front wheel traveled distance in steps
	phi = (odom_data_msg.stepAngleSteerStart + odom_data_msg.stepAngleSteerEnd)/2; //Get average front wheel steer angle (in steps)
	phi = (phi * 0.12 * microstepSteeringRatio * pi)/180;										//Convert step to radians according according to microstepping configuration, gear ratio and stepper motor ratio
 	
 	if(phi == 0){ //If not angular displacement
		//Calculate displacement in the robot base frame 		
 		frontWheelDistance = (tractionSteps * wheel_radius * microstepTractionRatio * pi)/200; //Front wheel distance, converted in meters
 		omega = 0.0;
 		dx = frontWheelDistance;
  		dy = 0.0;
 	}
 	else{
 		//Calculate displacement in the robot base frame
  		frontWheelDistance = (tractionSteps * wheel_radius * microstepTractionRatio * pi)/200;	//Front wheel distance, converted in meters
  		omega = frontWheelDistance * (sin(phi)/length);
		dx = length * (cos(phi)/sin(phi)) * sin(omega);
  		dy = length * (cos(phi)/sin(phi)) * (1-cos(omega));
 	}

  	//Add displacement to global displacement in the odometry frame
   x_pos += (cos(alpha) * dx - sin(alpha) * dy);
   y_pos += (sin(alpha) * dx + cos(alpha) * dy);
   alpha += omega; 

   if(alpha >= two_pi) alpha -= two_pi;
   if(alpha <= -two_pi) alpha += two_pi;
   
   //Calculate speeds
   vx = dx/dt;
	vy = dy/dt;
	vth = omega/dt;	
	
   geometry_msgs::Quaternion odom_quat = tf::createQuaternionMsgFromYaw(alpha);

   //Publish the transform over tf
   geometry_msgs::TransformStamped odom_trans;
   odom_trans.header.stamp = current_time;
   odom_trans.header.frame_id = "odom";
   odom_trans.child_frame_id = "base_link";

   odom_trans.transform.translation.x = x_pos;
   odom_trans.transform.translation.y = y_pos;
   odom_trans.transform.translation.z = 0.025;
   odom_trans.transform.rotation = odom_quat;

   //send the transform
   odom_broadcaster.sendTransform(odom_trans);

   //Publish the odometry message over ROS
   nav_msgs::Odometry odom;
   odom.header.stamp = current_time;
   odom.header.frame_id = "odom";

   //set the position
   odom.pose.pose.position.x = x_pos;
   odom.pose.pose.position.y = y_pos;
   odom.pose.pose.position.z = 0.025;
   odom.pose.pose.orientation = odom_quat;

   //set the velocity
   odom.child_frame_id = "base_link";
   odom.twist.twist.linear.x = vx;
   odom.twist.twist.linear.y = vy;
   odom.twist.twist.angular.z = vth;

   //publish the message
   odom_pub.publish(odom); 
   
   //Set the joint message
   joints.name.resize(17);
	joints.position.resize(17);
	joints.name[0] = "base_link_to_carter";
	joints.name[1] = "base_link_to_front_wheel_support";
	joints.name[2] = "front_wheel_support_to_motor";
	joints.name[3] = "front_wheel_support_to_front_wheel";
	joints.name[4] = "base_link_to_left_rear_wheel";
	joints.name[5] = "base_link_to_right_rear_wheel";
	joints.name[6] = "base_link_to_front_camera_support";
	joints.name[7] = "front_camera_support_to_front_camera";
	joints.name[8] = "front_camera_to_front_camera_img_origin";
	joints.name[9] = "base_link_to_rear_camera_support";
	joints.name[10] = "rear_camera_support_to_rear_camera";
	joints.name[11] = "rear_camera_to_rear_camera_img_origin";
	joints.name[12] = "base_link_to_slider_base";
	joints.name[13] = "slider_base_to_slider";
	joints.name[14] = "slider_to_slider_camera_support";
	joints.name[15] = "slider_camera_support_to_slider_camera";
	joints.name[16] = "slider_camera_to_slider_camera_img_origin";
	//Init joint message
	joints.position[0] = 0;				//"base_link_to_carter", fixed
   joints.position[1] = phi;			//base_link_to_front_wheel_support"; front wheel angle Phi  
   joints.position[2] = 0;				//"front_wheel_support_to_motor", fixed
   joints.position[3] = 0;				//"front_wheel_support_to_front_wheel", fixed
   joints.position[4] = 0;				//"base_link_to_left_rear_wheel", fixed
   joints.position[5] = 0;				//"base_link_to_right_rear_wheel", fixed   
   joints.position[6] = 0;				//"base_link_to_front_camera_support", fixed
	joints.position[7] = 0;				//"front_camera_support_to_front_camera", fixed
	joints.position[8] = 0;				//"front_camera_to_front_camera_img_origin", fixed
	joints.position[9] = 0;				//"base_link_to_rear_camera_support", fixed
	joints.position[10] = 0;			//"rear_camera_support_to_rear_camera", fixed
	joints.position[11] = 0;			//"rear_camera_to_rear_camera_img_origin", fixed  
	joints.position[12] = 0;			//"base_link_to_slider_base", TODO
	joints.position[13] = 0;			//"slider_base_to_slider", TODO
	joints.position[14] = 0;			//"slider_to_slider_camera_support", fixed
	joints.position[15] = 0;			//"slider_camera_support_to_slider_camera", fixed
	joints.position[16] = 0;			//"slider_camera_to_slider_camera_img_origin", fixed
	
	//Publish joint message to joint state publisher
	odom_joint_pub.publish(joints);

	}

private:
	ros::NodeHandle n; 
	ros::Publisher odom_pub;							//Create odometry publisher
	ros::Subscriber odom_data_sub;					//Create odometry data subcriber
	tf::TransformBroadcaster odom_broadcaster;	//Create odometry transform broadcaster
	ros::Publisher odom_joint_pub;
		
	//Create joint publisher message
	sensor_msgs::JointState joints;
	
	ros::Time current_time;

};//End of class SubscribeAndPublish

int main(int argc, char **argv)
{
	ros::init(argc, argv, "scriba_odometry_broadcaster");
	
	//Create an object of class SubscribeAndPublish that will take care of everything
	SubscribeAndPublish SAPObject;
	
	ros::Rate r(rate);
	ros::spin();

	return 0;
}

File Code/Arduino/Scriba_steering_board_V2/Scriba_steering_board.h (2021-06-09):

#include <AccelStepper.h>
#include <MultiStepper.h>
#include <ros.h>
#include <scriba_msgs/mot_cmd.h>
#include <scriba_msgs/data_odom.h>
#include <scriba_msgs/front_wheel_calibration.h>
#include <std_msgs/String.h>
#include <ros/time.h>
#include "scriba_drive_log_msgs.h"

using scriba_msgs::front_wheel_calibration;

//Start ROS node handle
ros::NodeHandle nh; //ROS buffer size /!\ an high buffer size can fill the Arduino's memory. Optimizing the buffer size is capital

int angleStepCmd = 0;
int tractionSpeedCmd = 0;
long steerAngleStepsStart = 0;
long steerAngleStepsEnd = 0;
long steerAnglePotStart;
long steerAnglePotEnd;
int angleStep = 0;              //Front wheel angle in steps
int tractionSpeed = 800;        //Traction stepper motor speed in steps/second
int steeringSpeed = 400;        //Steering stepper motor speed in steps/second
int tractionAcc = 350;    //Traction stepper motor acceleration in steps/second/second
int steeringAcc = 200;    //Traction stepper motor acceleration in steps/second/second

//----------------
// Time variables
//----------------
const int looptime = 100;             //Looptime in millisecond
unsigned long lastMilli = 0;
unsigned long lastCommMillis = 0;
const unsigned long noCommDurationMax = 1500;   //Set the max time for the robot to run without motor commands

//-------------
// Pin numbers
//-------------
const int tractionDirPin = 7;
const int steeringDirPin = 6;
const int tractionStepPin = 10;
const int steeringStepPin = 9;
const int tractionSleepPin = A1;
const int steeringSleepPin = A0;
const int tractionEnablePin = A4;
const int steeringEnablePin = 8;
const int tractionResetPin = 13;
const int steeringResetPin = 12;
const int steeringMSLeftPin = A2;   //Steering left microswitch pin
const int steeringMSRightPin = A3;  //Steering right microswitch pin
const int EMStopPin = A5;           //Emergency stop signal pin
const int steeringPotPin = A7;      //Steering angle potentiometer data pin

byte mode = 0;                      /* Driving mode. 0 is for standard mode (ajust front wheel angle while moving)
                                      and 1 for printing mode (ajust front wheel angle and then move) */
                    
long minSteeringStep = -2000;       //End position right step value
long maxSteeringStep = 2000;        //End position left step value
float microstepSteeringRatio = 0.5; //Microstepping configuration for steering motor
float microstepTractionRatio = 0.5; //Microstepping configuration for traction motor
float potSteeringRatio = 251;       //Potentiometer ticks per rad
const float wheelRadius = 0.025;    //Front wheel radius in meters
const float pi = 3.14159;           //It's just Pi, what did you expect?
//Compute ratio from potentiometer value to steering motor step
float stepsPerTick = (180/(0.12 * microstepSteeringRatio * pi)) / potSteeringRatio;robot

//Create stepper objects for steering and traction stepper motor
AccelStepper tractionStepper = AccelStepper(1, tractionStepPin, tractionDirPin);
AccelStepper steeringStepper = AccelStepper(1, steeringStepPin, steeringDirPin);
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

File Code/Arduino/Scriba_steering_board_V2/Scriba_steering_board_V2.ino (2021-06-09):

//This program is driving the Scriba robot according to received motor commands
//The robot first follows a steering calibration procedure before driving
//The program also includes an emergency button stop function that will prevent the robot from moving if the emergency signal is low
//Author: Robin Baran
//Email: r-baran@hotmail.fr

#include "Scriba_steering_board.h"

//____________________________________________________

void setup(){
  // Start motor control and ROS node
  setupController();
}

void loop(){
  // Run controller at set looprate
  runController();
  //status_msg.data = "board running";
  //status_pub.publish(&status_msg);
  nh.spinOnce();
}  

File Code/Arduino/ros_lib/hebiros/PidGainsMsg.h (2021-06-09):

#ifndef _ROS_hebiros_PidGainsMsg_h
#define _ROS_hebiros_PidGainsMsg_h

#include <stdint.h>
#include <string.h>
#include <stdlib.h>
#include "ros/msg.h"

namespace hebiros
{

  class PidGainsMsg : public ros::Msg
  {
    public:
      uint32_t name_length;
      typedef char* _name_type;
      _name_type st_name;
      _name_type * name;
      uint32_t kp_length;
      typedef float _kp_type;
      _kp_type st_kp;
      _kp_type * kp;
      uint32_t ki_length;
      typedef float _ki_type;
      _ki_type st_ki;
      _ki_type * ki;
      uint32_t kd_length;
      typedef float _kd_type;
      _kd_type st_kd;
      _kd_type * kd;
      uint32_t feed_forward_length;
      typedef float _feed_forward_type;
      _feed_forward_type st_feed_forward;
      _feed_forward_type * feed_forward;
      uint32_t dead_zone_length;
      typedef float _dead_zone_type;
      _dead_zone_type st_dead_zone;
      _dead_zone_type * dead_zone;
      uint32_t i_clamp_length;
      typedef float _i_clamp_type;
      _i_clamp_type st_i_clamp;
      _i_clamp_type * i_clamp;
      uint32_t punch_length;
      typedef float _punch_type;
      _punch_type st_punch;
      _punch_type * punch;
      uint32_t min_target_length;
      typedef float _min_target_type;
      _min_target_type st_min_target;
      _min_target_type * min_target;
      uint32_t max_target_length;
      typedef float _max_target_type;
      _max_target_type st_max_target;
      _max_target_type * max_target;
      uint32_t target_lowpass_length;
      typedef float _target_lowpass_type;
      _target_lowpass_type st_target_lowpass;
      _target_lowpass_type * target_lowpass;
      uint32_t min_output_length;
      typedef float _min_output_type;
      _min_output_type st_min_output;
      _min_output_type * min_output;
      uint32_t max_output_length;
      typedef float _max_output_type;
      _max_output_type st_max_output;
      _max_output_type * max_output;
      uint32_t output_lowpass_length;
      typedef float _output_lowpass_type;
      _output_lowpass_type st_output_lowpass;
      _output_lowpass_type * output_lowpass;
      uint32_t d_on_error_length;
      typedef bool _d_on_error_type;
      _d_on_error_type st_d_on_error;
      _d_on_error_type * d_on_error;

    PidGainsMsg():
      name_length(0), st_name(), name(nullptr),
      kp_length(0), st_kp(), kp(nullptr),
      ki_length(0), st_ki(), ki(nullptr),
      kd_length(0), st_kd(), kd(nullptr),
      feed_forward_length(0), st_feed_forward(), feed_forward(nullptr),
      dead_zone_length(0), st_dead_zone(), dead_zone(nullptr),
      i_clamp_length(0), st_i_clamp(), i_clamp(nullptr),
      punch_length(0), st_punch(), punch(nullptr),
      min_target_length(0), st_min_target(), min_target(nullptr),
      max_target_length(0), st_max_target(), max_target(nullptr),
      target_lowpass_length(0), st_target_lowpass(), target_lowpass(nullptr),
      min_output_length(0), st_min_output(), min_output(nullptr),
      max_output_length(0), st_max_output(), max_output(nullptr),
      output_lowpass_length(0), st_output_lowpass(), output_lowpass(nullptr),
      d_on_error_length(0), st_d_on_error(), d_on_error(nullptr)
    {
    }

    virtual int serialize(unsigned char *outbuffer) const override
    {
      int offset = 0;
      *(outbuffer + offset + 0) = (this->name_length >> (8 * 0)) & 0xFF;
      *(outbuffer + offset + 1) = (this->name_length >> (8 * 1)) & 0xFF;
      *(outbuffer + offset + 2) = (this->name_length >> (8 * 2)) & 0xFF;
      *(outbuffer + offset + 3) = (this->name_length >> (8 * 3)) & 0xFF;
      offset += sizeof(this->name_length);
      for( uint32_t i = 0; i < name_length; i++){
      uint32_t length_namei = strlen(this->name[i]);
      varToArr(outbuffer + offset, length_namei);
      offset += 4;
      memcpy(outbuffer + offset, this->name[i], length_namei);
      offset += length_namei;
      }
      *(outbuffer + offset + 0) = (this->kp_length >> (8 * 0)) & 0xFF;
      *(outbuffer + offset + 1) = (this->kp_length >> (8 * 1)) & 0xFF;
      *(outbuffer + offset + 2) = (this->kp_length >> (8 * 2)) & 0xFF;
      *(outbuffer + offset + 3) = (this->kp_length >> (8 * 3)) & 0xFF;
      offset += sizeof(this->kp_length);
      for( uint32_t i = 0; i < kp_length; i++){
      offset += serializeAvrFloat64(outbuffer + offset, this->kp[i]);
      }
      *(outbuffer + offset + 0) = (this->ki_length >> (8 * 0)) & 0xFF;
      *(outbuffer + offset + 1) = (this->ki_length >> (8 * 1)) & 0xFF;
      *(outbuffer + offset + 2) = (this->ki_length >> (8 * 2)) & 0xFF;
      *(outbuffer + offset + 3) = (this->ki_length >> (8 * 3)) & 0xFF;
      offset += sizeof(this->ki_length);
      for( uint32_t i = 0; i < ki_length; i++){
      offset += serializeAvrFloat64(outbuffer + offset, this->ki[i]);
      }
      *(outbuffer + offset + 0) = (this->kd_length >> (8 * 0)) & 0xFF;
      *(outbuffer + offset + 1) = (this->kd_length >> (8 * 1)) & 0xFF;
      *(outbuffer + offset + 2) = (this->kd_length >> (8 * 2)) & 0xFF;
      *(outbuffer + offset + 3) = (this->kd_length >> (8 * 3)) & 0xFF;
      offset += sizeof(this->kd_length);
      for( uint32_t i = 0; i < kd_length; i++){
      offset += serializeAvrFloat64(outbuffer + offset, this->kd[i]);
      }
      *(outbuffer + offset + 0) = (this->feed_forward_length >> (8 * 0)) & 0xFF;
      *(outbuffer + offset + 1) = (this->feed_forward_length >> (8 * 1)) & 0xFF;
      *(outbuffer + offset + 2) = (this->feed_forward_length >> (8 * 2)) & 0xFF;
      *(outbuffer + offset + 3) = (this->feed_forward_length >> (8 * 3)) & 0xFF;
      offset += sizeof(this->feed_forward_length);
      for( uint32_t i = 0; i < feed_forward_length; i++){
      offset += serializeAvrFloat64(outbuffer + offset, this->feed_forward[i]);
      }
      *(outbuffer + offset + 0) = (this->dead_zone_length >> (8 * 0)) & 0xFF;
      *(outbuffer + offset + 1) = (this->dead_zone_length >> (8 * 1)) & 0xFF;
      *(outbuffer + offset + 2) = (this->dead_zone_length >> (8 * 2)) & 0xFF;
      *(outbuffer + offset + 3) = (this->dead_zone_length >> (8 * 3)) & 0xFF;
      offset += sizeof(this->dead_zone_length);
      for( uint32_t i = 0; i < dead_zone_length; i++){
      offset += serializeAvrFloat64(outbuffer + offset, this->dead_zone[i]);
      }
      *(outbuffer + offset + 0) = (this->i_clamp_length >> (8 * 0)) & 0xFF;
      *(outbuffer + offset + 1) = (this->i_clamp_length >> (8 * 1)) & 0xFF;
      *(outbuffer + offset + 2) = (this->i_clamp_length >> (8 * 2)) & 0xFF;
      *(outbuffer + offset + 3) = (this->i_clamp_length >> (8 * 3)) & 0xFF;
      offset += sizeof(this->i_clamp_length);
      for( uint32_t i = 0; i < i_clamp_length; i++){
      offset += serializeAvrFloat64(outbuffer + offset, this->i_clamp[i]);
      }
      *(outbuffer + offset + 0) = (this->punch_length >> (8 * 0)) & 0xFF;
      *(outbuffer + offset + 1) = (this->punch_length >> (8 * 1)) & 0xFF;
      *(outbuffer + offset + 2) = (this->punch_length >> (8 * 2)) & 0xFF;
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

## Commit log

2019-09-04 Minor changes & spell check
    [Part List.xlsx]
2019-09-30 Folders reorganized
    [2.54_pin_female_headers.SLDPRT, 2.54_pin_male_headers.SLDPRT, Ball_Conveyor_Roller_CY-8H.SLDPRT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]
2021-02-11 Add angle kalman filter library
2021-02-11 Add steering angle potentiometer in arduino firmware
2021-02-14 Add angle kalman filter in odometry broadcaster
2021-02-16 Refactor odometry broadcaster code and add params
2021-02-26 Add steering potentiometer and comments to message files
2021-02-26 Reinsert steering board firmware V2 as independant folder
2021-06-08 Add new Arduino firmware
2021-06-08 Move ROS code to dedicated repo
    [camera.STL, camera_support.STL, carter.STL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]
2021-10-26 Add steering potentiometer to CAD
    [91A1A-B28.stp.SLDPRT, Rear_base_support.STL, calibration_rig.SLDASM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]
2021-10-26 Add calibration rig
    [calibration_rig.SLDDRW, end_position_steering_shaft.STL]
2021-10-26 Add missing CAD updates after adding steering potentiometer
    [2.54_pin_female_headers.SLDPRT, 2.54_pin_male_headers.SLDPRT, Ball_Conveyor_Roller_CY-8H.SLDPRT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]
